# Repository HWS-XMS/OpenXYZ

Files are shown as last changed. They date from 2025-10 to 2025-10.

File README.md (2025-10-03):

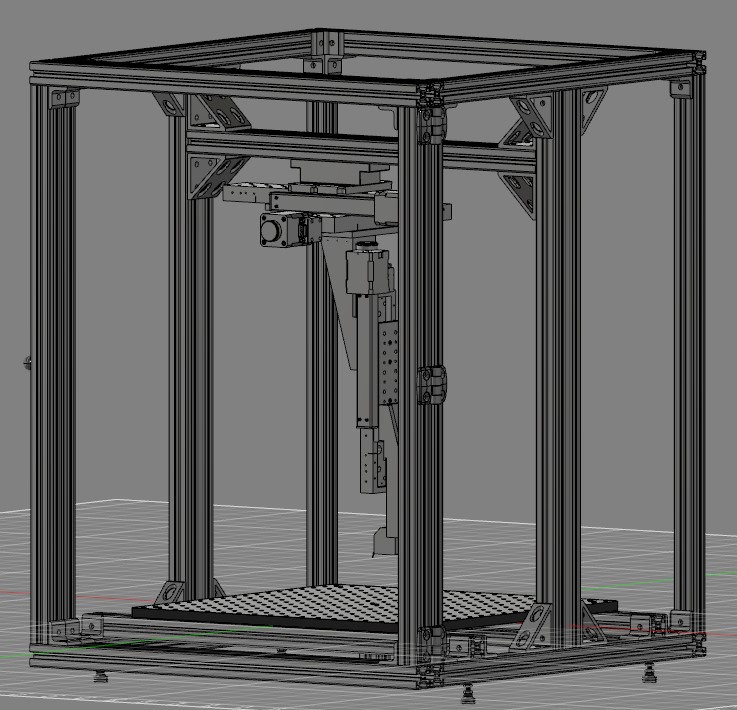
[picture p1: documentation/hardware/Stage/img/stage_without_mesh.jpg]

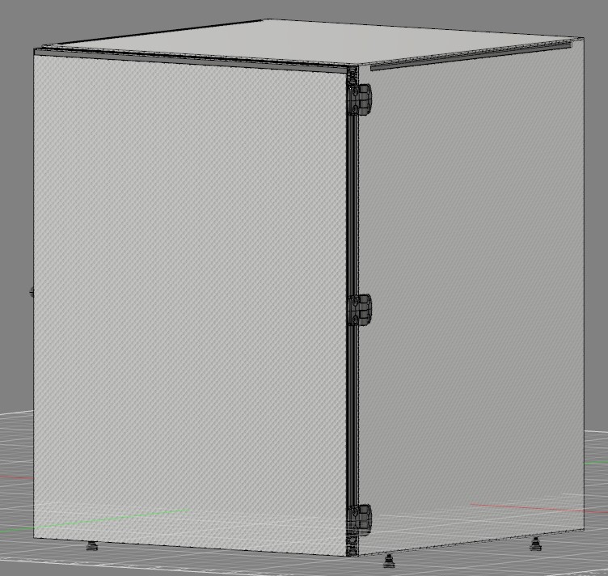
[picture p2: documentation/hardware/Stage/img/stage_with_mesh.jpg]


# Open-XYZ
An Open-Source Positioning System for Physical Attacks Exhibiting Spatial Resolution

**Author:** Marvin Sass
**Contributors:** Jakob Frömbgen, Olaf Durban

## Installation

### 1. Clone Repository with Submodules

```bash
git clone --recursive git@github.com:HWS-XMS/OpenXYZ.git
cd OpenXYZ
```

If you already cloned without `--recursive`:
```bash
git submodule update --init --recursive
```

### 2. Install Python Dependencies

**Host Computer:**
```bash
# Create and activate virtual environment (recommended)
python3 -m venv venv
source venv/bin/activate  # macOS/Linux
# .\venv\Scripts\activate  # Windows

# Install dependencies
pip3 install -r requirements.txt

# Install CoordinatePaths package from submodule
pip3 install -e CoordinatePaths/
```

**Raspberry Pi (for running the bridge server):**
```bash
pip3 install -r requirements-rpi.txt
```

## Path Generation

Path generation is handled by the separate [CoordinatePaths](https://github.com/HWS-XMS/CoordinatePaths) package (included as a git submodule). Three path types are available:

**RectangularPath** - Snake-like raster scanning:
```
(x_max, y_max)
  END +-->+-->+-->#
      ^   |   |   |
      +<--+<--+<--+
      |   |   |   ^
      +-->+-->+-->+
      ^   |   |   |
      +<--+<--+<--# START
                (0,0)
```

**CircularPath** - Spiral scanning from center outward

**PolygonPath** - Raster scanning within arbitrary polygonal areas

## Stage Positioning
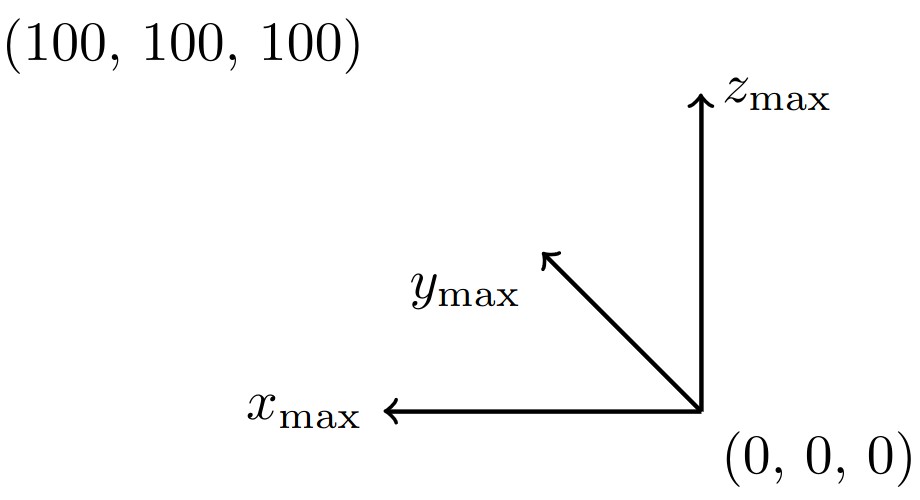
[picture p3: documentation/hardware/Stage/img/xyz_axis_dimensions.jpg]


The coordinate system origin is located at the bottom right (0, 0, 0). All coordinates are in millimeters. The stage supports 3-axis movement:
- **X/Y axes**: Horizontal positioning of probe
- **Z axis**: Height adjustment above target

## Usage

Complete working examples are available in the `examples/` directory:
- `basic_scan_with_callback.py` - Rectangular scanning with measurement callback
- `circular_scan_example.py` - Circular/spiral scanning pattern
- `read_scan_results.py` - Loading and processing saved measurement data

### Basic Example

```python
from openxyz.xyz_stage import Stage
from openxyz.marlin import Marlin
from coordinate_paths import RectangularPath
import decimal
import pickle

# Initialize stage
stage = Stage(Marlin(ip="openxyz"))  # or use IP address like "192.168.1.100"

# Create scanning path
path = RectangularPath(
    start_xy=(decimal.Decimal('0'), decimal.Decimal('0')),
    end_xy=(decimal.Decimal('10'), decimal.Decimal('10')),
    step_size_x=decimal.Decimal('0.5'),
    step_size_y=decimal.Decimal('0.5')
)

# Set probe height
stage.z = decimal.Decimal('40')

# Scan and measure
with open('results.pckl', 'wb') as f:
    for coordinate in path:
        # Move to position
        stage.x = coordinate[0]
        stage.y = coordinate[1]

        # Your measurement code here
        data = your_measurement_function()

        # Save with position
        pickle.dump((coordinate, data), f)
```

## Hardware Components

- **Motion Control**: Marlin firmware on BTT Manta M8P board
- **Actuators**: Motorized linear stages with TMC stepper drivers
- **Position Feedback**: LS7366R encoder chips with optical encoders
- **Control Interface**: Raspberry Pi running Flask server (optional bridge)

See `documentation/hardware/` for detailed hardware documentation.

## Architecture

**Host Computer** (your workstation):
- Runs measurement scripts
- Generates scan paths using CoordinatePaths
- Sends G-code commands to stage via HTTP

**Raspberry Pi** (optional bridge, runs `openxyz/rpi.py`):
- Flask HTTP server
- Converts HTTP requests to serial G-code
- Reads encoder positions via SPI
- Direct connection to Marlin controller

**Marlin Controller** (BTT Manta M8P):
- Executes G-code movement commands
- Controls stepper motors via TMC drivers
- Handles position tracking and limits

## License

MIT License

## Repository

https://github.com/HWS-XMS/OpenXYZ

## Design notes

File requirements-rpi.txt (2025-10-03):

# Open-XYZ Requirements (Raspberry Pi)
# Install with: pip install -r requirements-rpi.txt
#
# The Raspberry Pi runs the Flask server (rpi.py) that bridges HTTP to serial/encoder.
# Path generation and visualization happen on the host computer, not on the Pi.

# Core dependencies
pyserial>=3.5.0        # Serial communication with Marlin controller

# Raspberry Pi specific dependencies
RPi.GPIO>=0.7.1        # GPIO control for encoder chip select pins
spidev>=3.6.0          # SPI communication with LS7366R encoder chips
flask>=2.3.0           # HTTP server for Marlin/encoder API endpoints

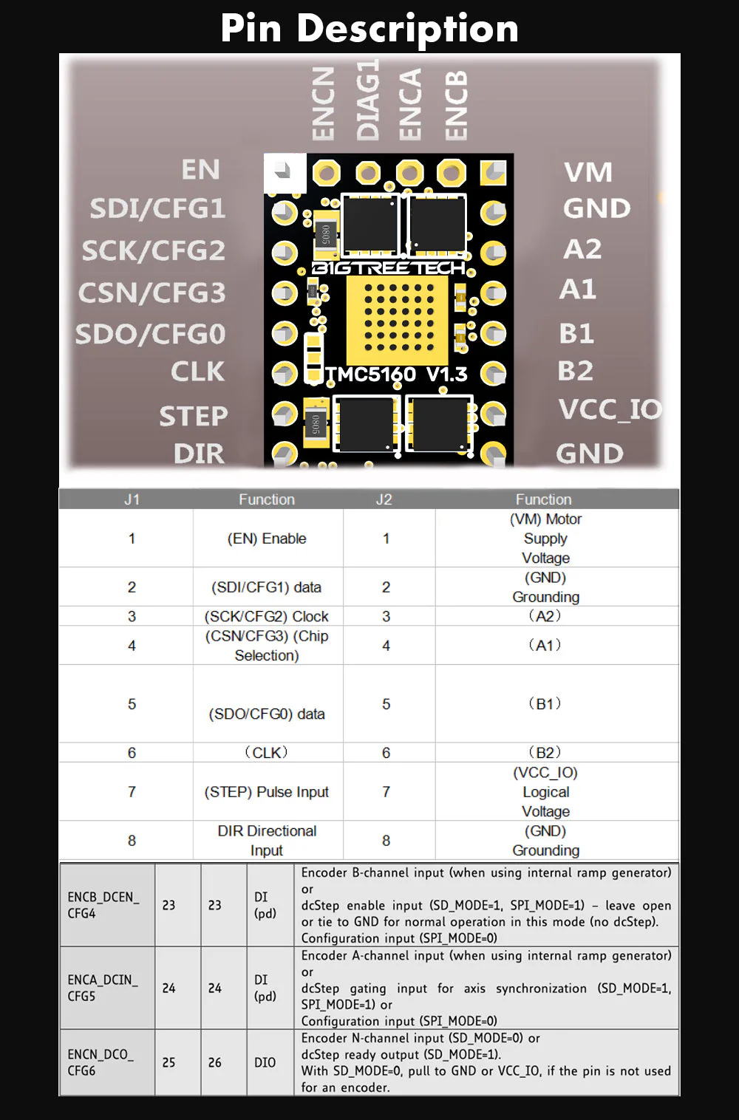
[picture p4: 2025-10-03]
documentation/hardware/TMC Drivers/TMC5160-data-sheet.webp

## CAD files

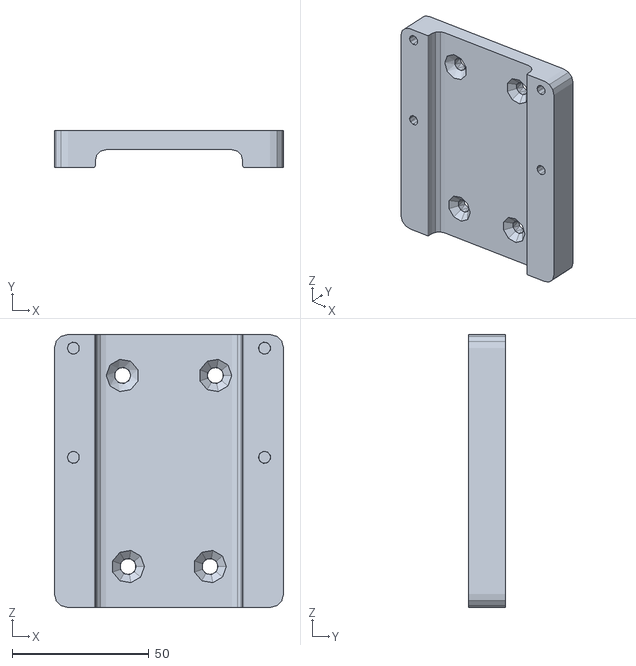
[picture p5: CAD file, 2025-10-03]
documentation/hardware/Chipshouter/cs_mount_bottom.stl
84.0 x 13.5 x 100.0

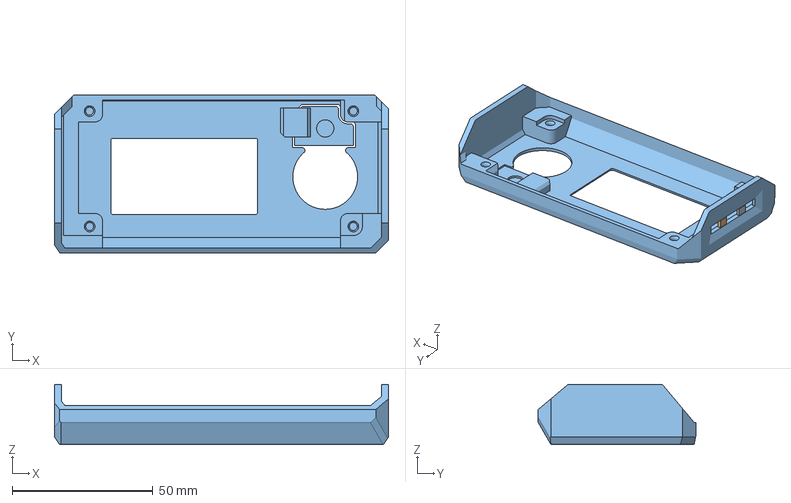
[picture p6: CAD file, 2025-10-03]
documentation/hardware/Display/new_cancel_button.3mf
118.7 x 56.0 x 21.5 mm
minidisplayhousing_v3 (1)
minidisplayhousing_v3 (2)
minidisplayhousing_v3

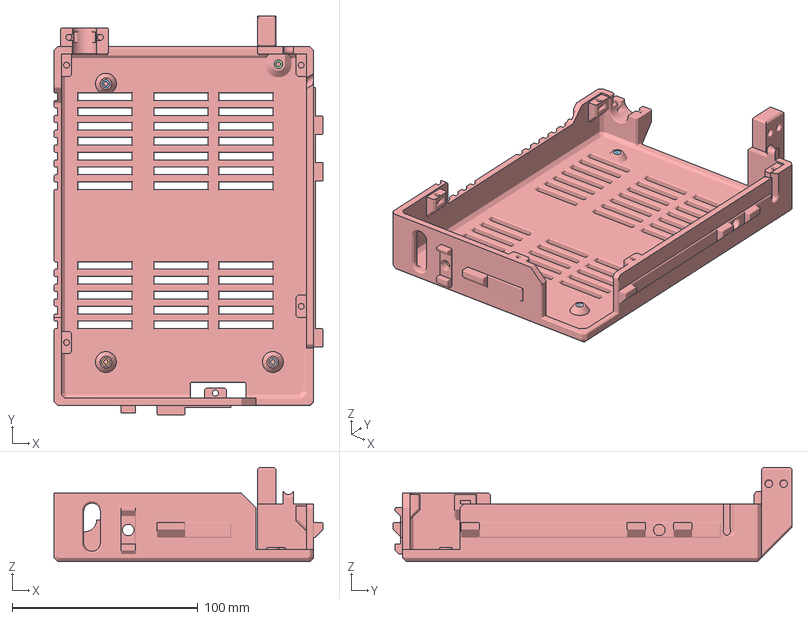
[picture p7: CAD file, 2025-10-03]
documentation/hardware/Manta Board/smaller_holes.3mf
145.0 x 214.9 x 50.7 mm
M8P Caribou - Unterteil

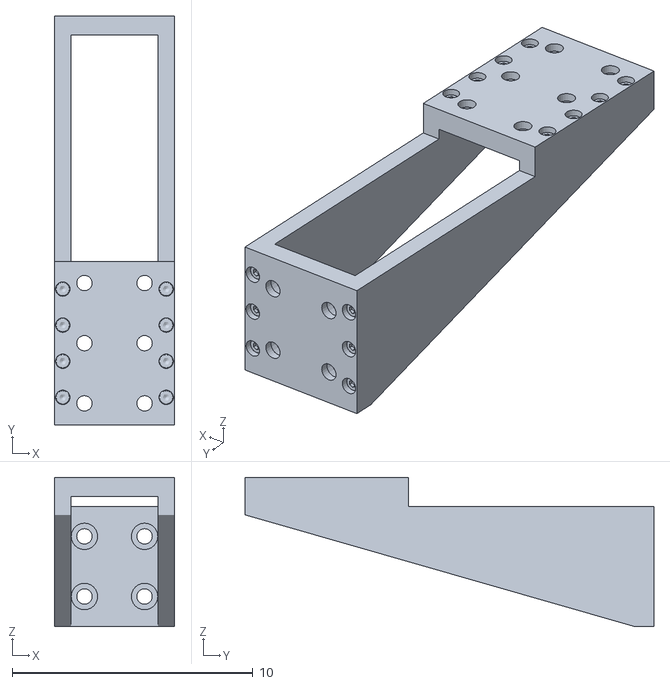
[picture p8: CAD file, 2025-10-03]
documentation/hardware/Stage/2AB175_90_degree_angle_bracket.obj
5.00 x 17.0 x 6.20

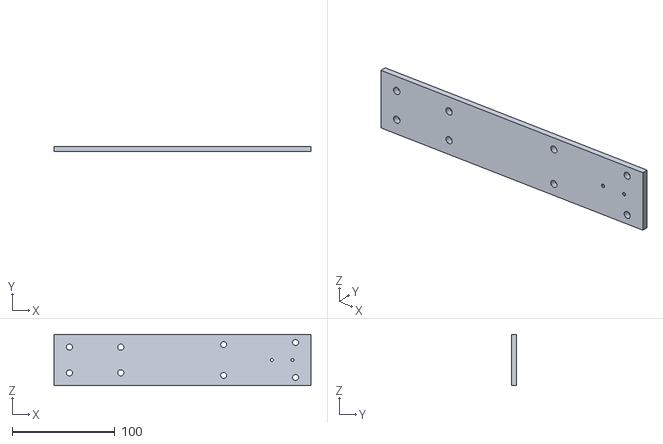
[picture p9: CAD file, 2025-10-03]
documentation/hardware/Chipshouter/cs_adapter.stl
250.0 x 5.00 x 50.0

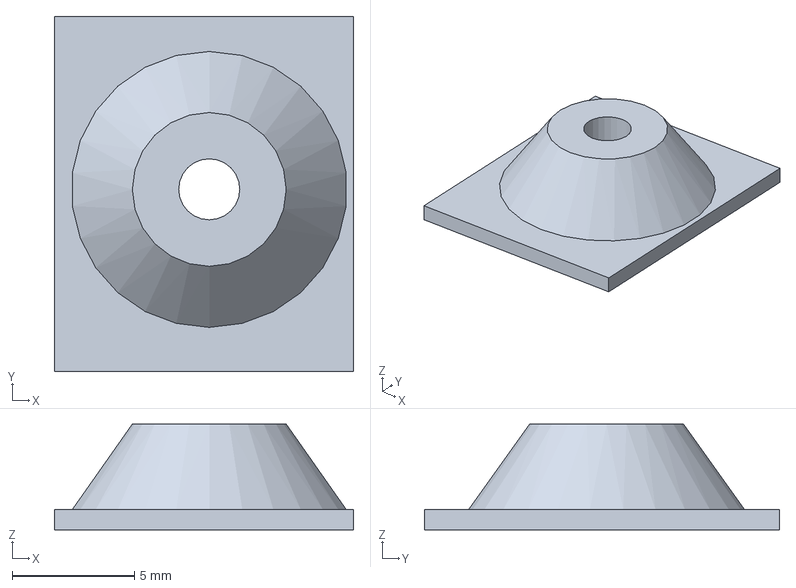
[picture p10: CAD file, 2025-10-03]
documentation/hardware/Manta Board/hole_test.3mf
12.3 x 14.5 x 4.34 mm

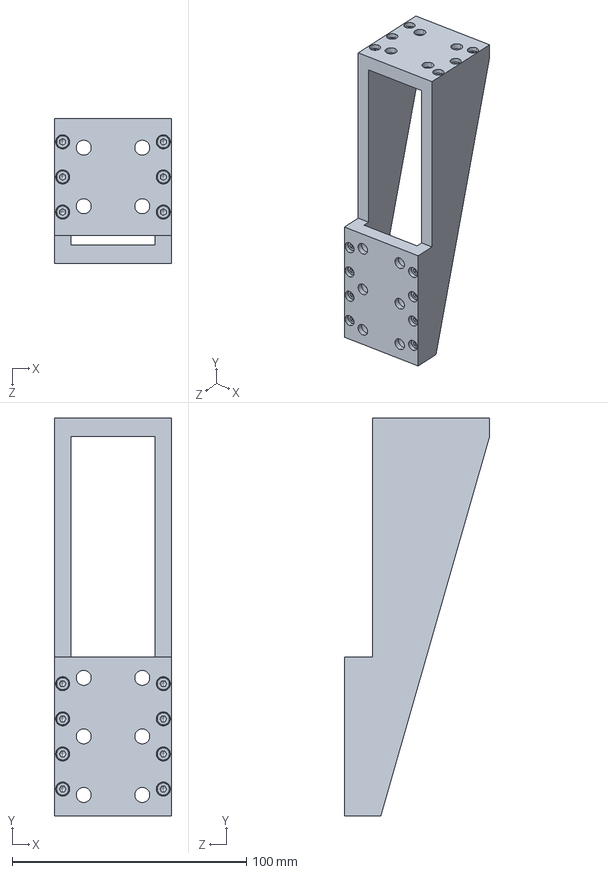
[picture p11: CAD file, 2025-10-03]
documentation/hardware/Stage/2AB175.STEP
50.0 x 170.0 x 62.0 mm

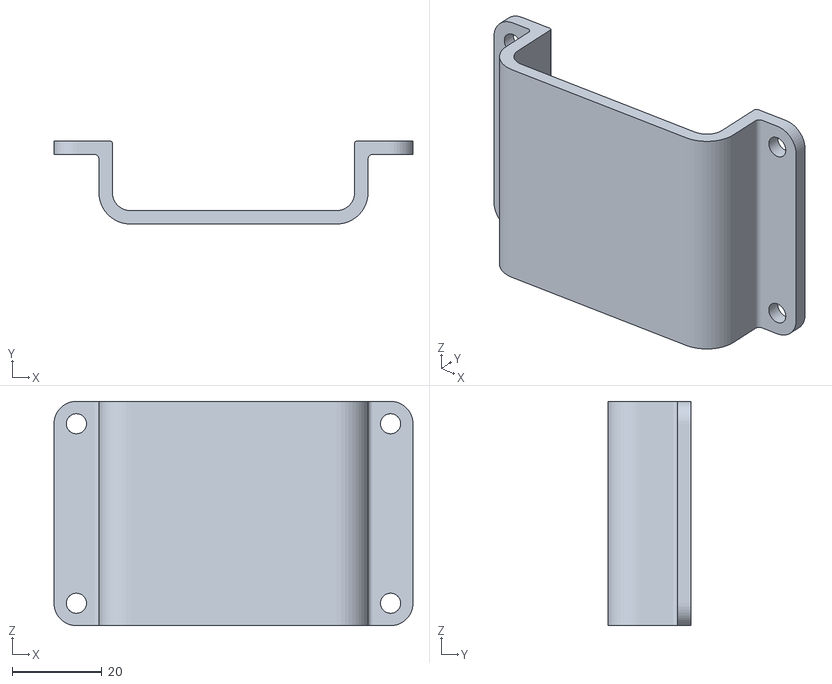
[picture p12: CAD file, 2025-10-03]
documentation/hardware/Chipshouter/cs_mount_top.stl
80.0 x 18.5 x 50.0

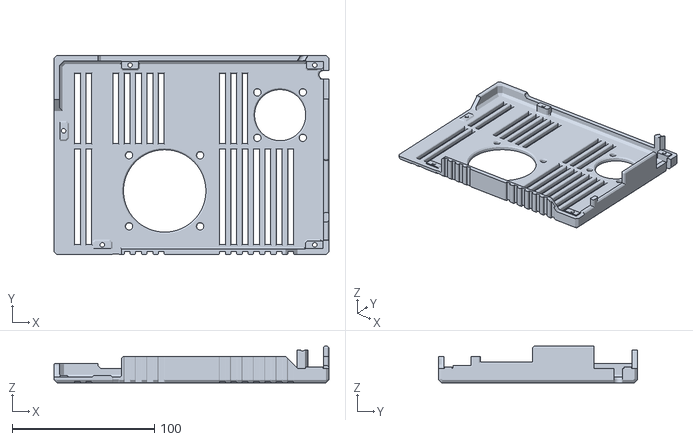
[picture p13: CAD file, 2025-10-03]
documentation/hardware/Manta Board/M8P Caribou - Deckel.stl
193.5 x 140.0 x 25.7

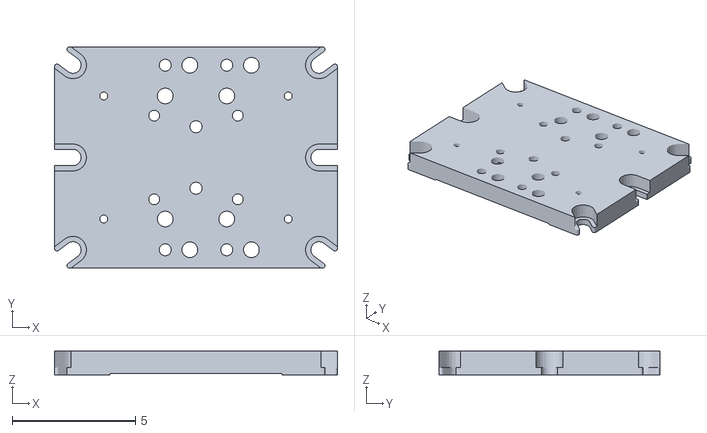
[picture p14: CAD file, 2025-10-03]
documentation/hardware/Stage/3UBP175__Baseplate_for_linear_actuators.obj
11.5 x 9.00 x 0.97

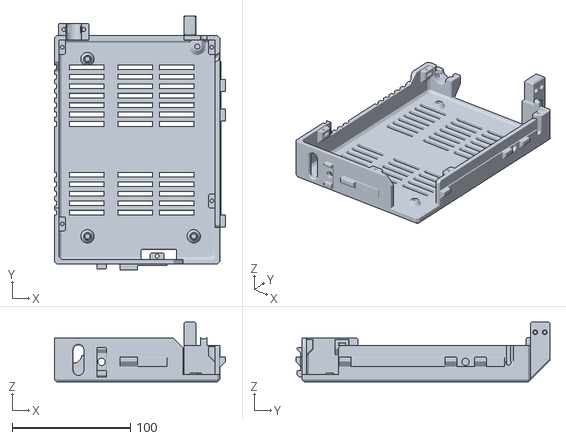
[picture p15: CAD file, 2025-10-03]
documentation/hardware/Manta Board/M8P Caribou - Unterteil.stl
145.0 x 214.9 x 50.7

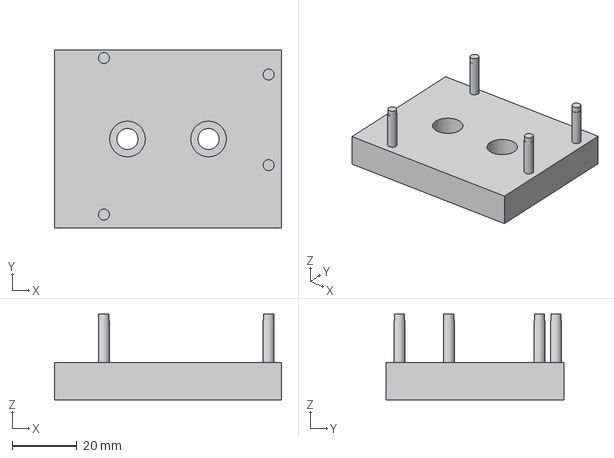
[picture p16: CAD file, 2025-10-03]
documentation/hardware/Stage/simple_Arduino_UNO_mount.3mf
70.0 x 55.0 x 26.5 mm

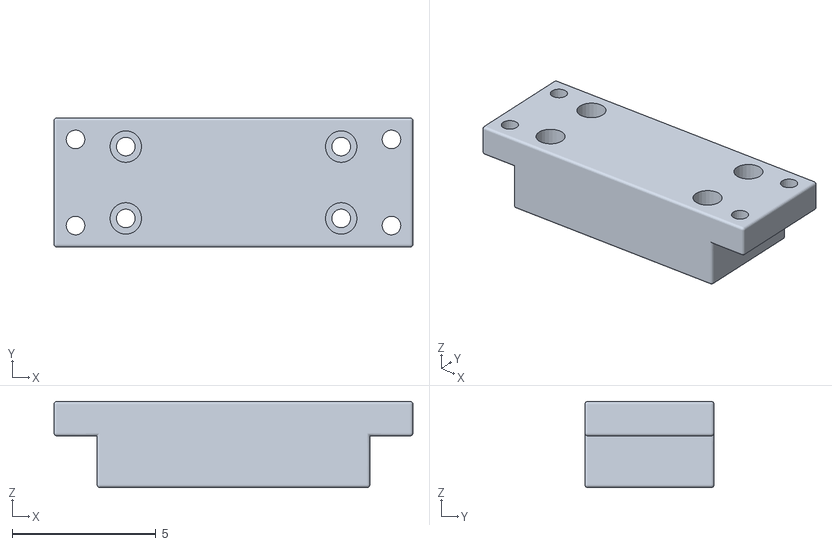
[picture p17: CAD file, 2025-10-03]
documentation/hardware/Stage/adapter_v4.obj
12.5 x 4.50 x 3.00

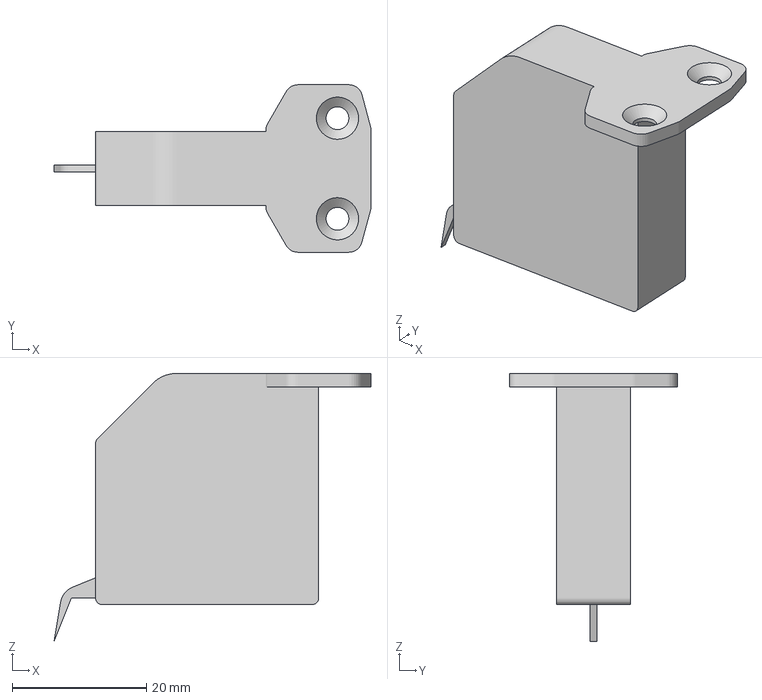
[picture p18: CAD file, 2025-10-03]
documentation/hardware/Stage/Probe Dummy 3D model 6.2x5.5 ICR v1.3mf
47.3 x 25.0 x 40.0 mm

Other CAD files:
documentation/hardware/Display/minidisplayhousing_v3.stl
documentation/hardware/Stage/3UBP175.STEP
documentation/hardware/Stage/Halterung Probe v3.3mf
documentation/hardware/Stage/Probe Dummy 3D model 6.2x5.5 ICR v1.obj

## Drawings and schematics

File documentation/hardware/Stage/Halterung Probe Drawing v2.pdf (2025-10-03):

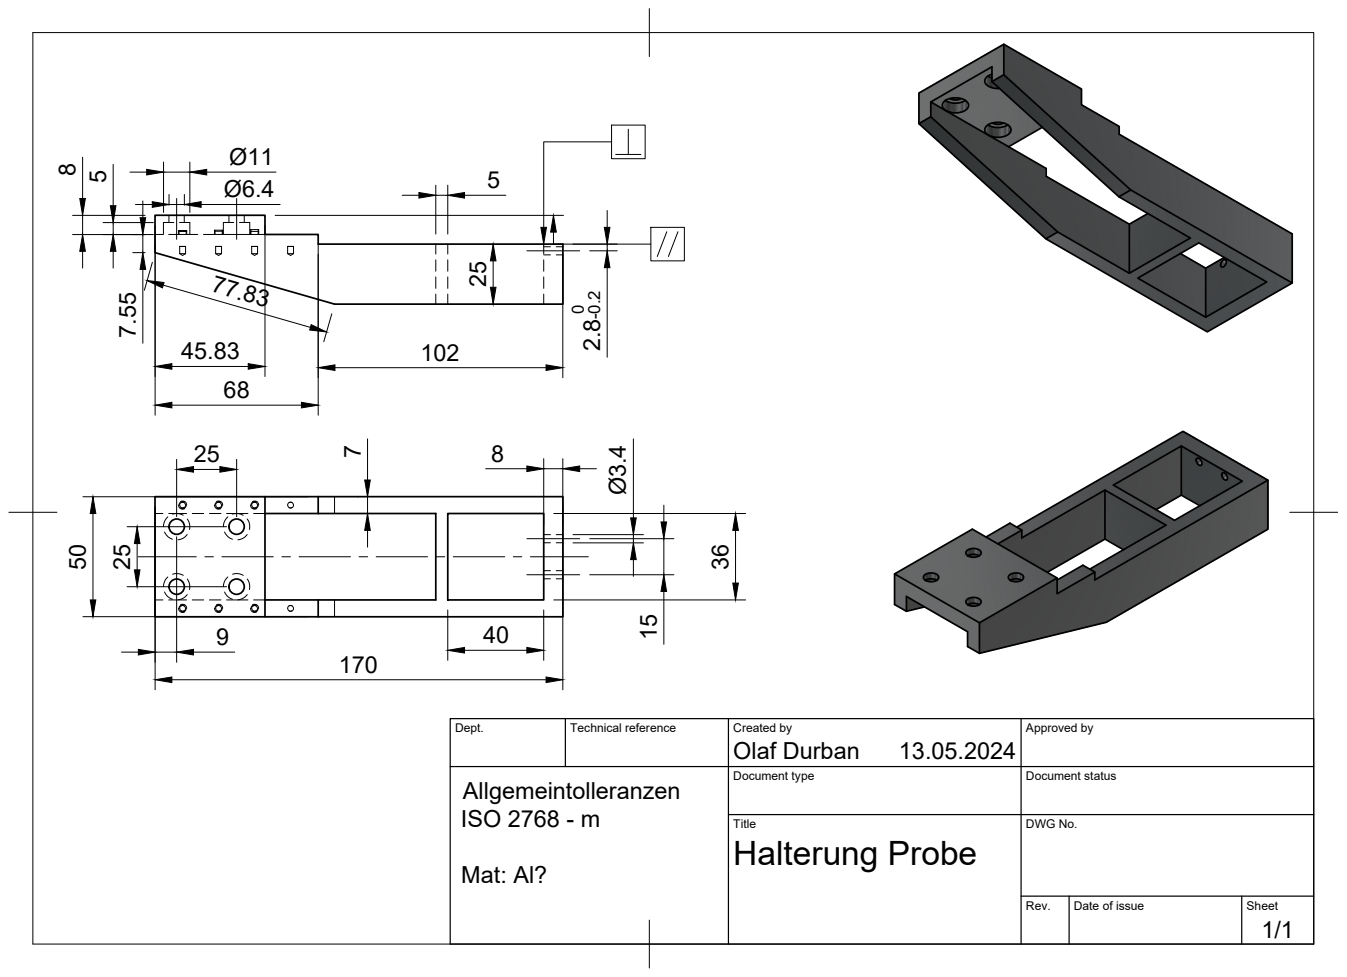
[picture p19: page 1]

Dept. | Technical reference | Created by Olaf Durban 13.05.2024 | Approved by

Allgemeintolleranzen ISO 2768 - m Mat: Al? | | Document type | Document status

Title Halterung Probe | DWG No.

Rev. | Date of issue | Sheet 1/1

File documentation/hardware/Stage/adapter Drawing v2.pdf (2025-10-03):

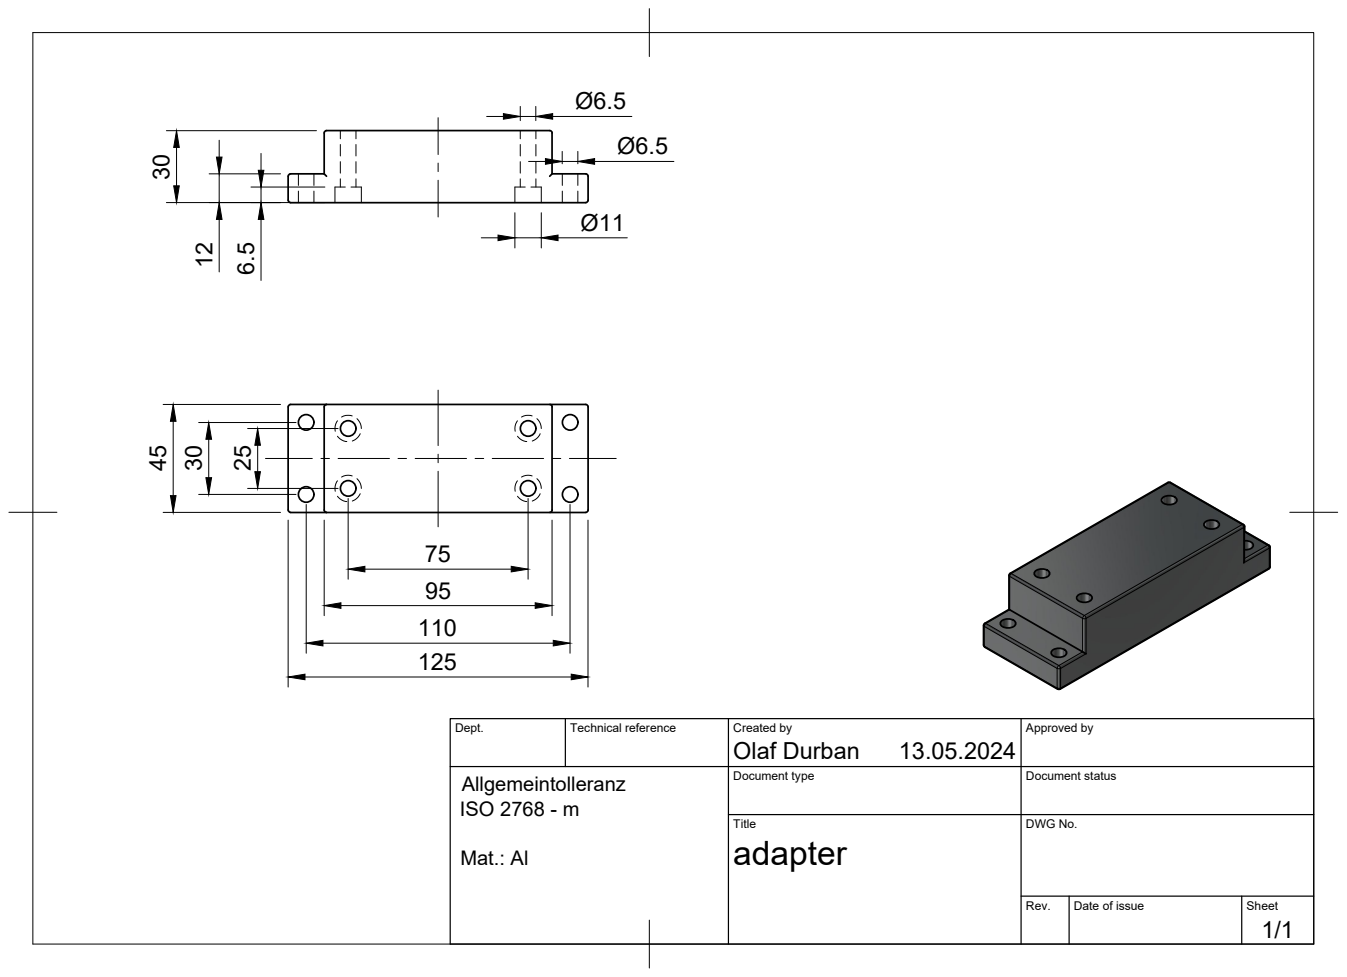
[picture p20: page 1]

Dept. | Technical reference | Created by Olaf Durban 13.05.2024 | Approved by

Allgemeintolleranz ISO 2768 - m Mat.: Al | | Document type | Document status

Title adapter | DWG No.

Rev. | Date of issue | Sheet 1/1

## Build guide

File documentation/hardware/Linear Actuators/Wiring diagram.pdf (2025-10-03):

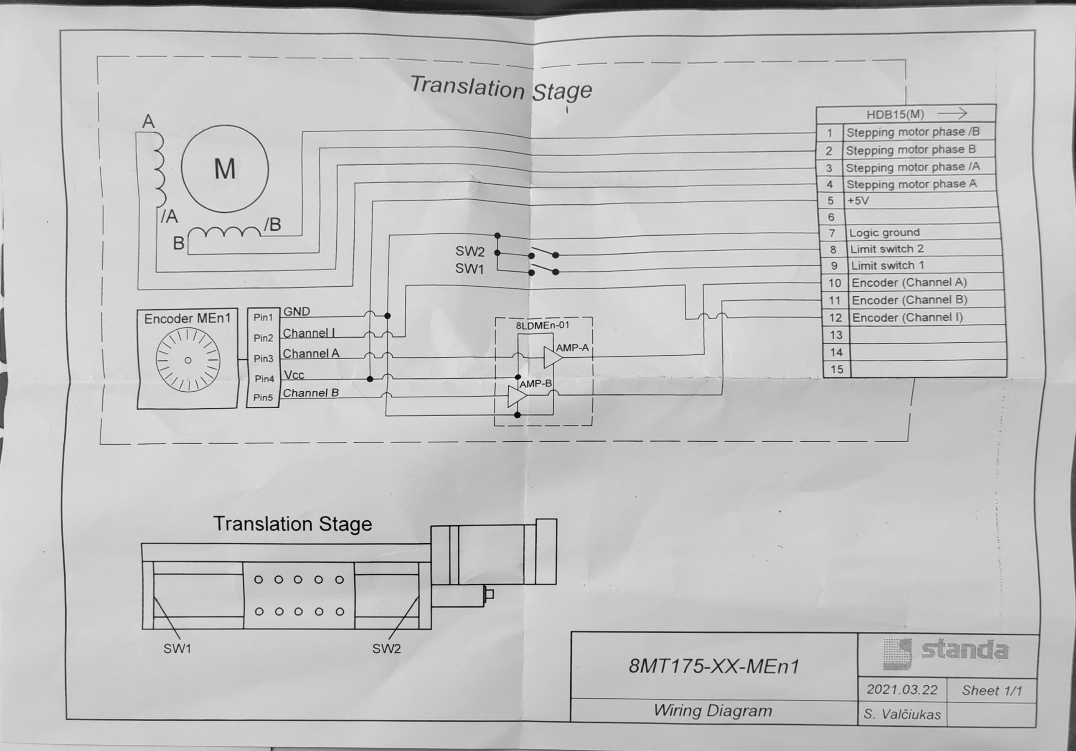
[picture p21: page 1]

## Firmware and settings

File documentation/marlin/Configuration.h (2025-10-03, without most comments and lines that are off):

#pragma once
#define CONFIGURATION_H_VERSION 02010300
#define STRING_CONFIG_H_AUTHOR "(none, default config)" // Who made the changes.
  #define MOTHERBOARD BOARD_BTT_MANTA_M8P_V2_0
#define SERIAL_PORT -1
#define BAUDRATE 250000
#define X_DRIVER_TYPE  TMC5160
#define Y_DRIVER_TYPE  TMC5160
#define Z_DRIVER_TYPE  TMC5160
#define EXTRUDERS 0
#define DEFAULT_NOMINAL_FILAMENT_DIA 1.75
#define TEMP_SENSOR_0 1
#define TEMP_SENSOR_1 0
#define TEMP_SENSOR_2 0
#define TEMP_SENSOR_3 0
#define TEMP_SENSOR_4 0
#define TEMP_SENSOR_5 0
#define TEMP_SENSOR_6 0
#define TEMP_SENSOR_7 0
#define TEMP_SENSOR_BED 0
#define TEMP_SENSOR_PROBE 0
#define TEMP_SENSOR_CHAMBER 0
#define TEMP_SENSOR_COOLER 0
#define TEMP_SENSOR_BOARD 0
#define TEMP_SENSOR_SOC 0
#define TEMP_SENSOR_REDUNDANT 0
#define DUMMY_THERMISTOR_998_VALUE  25
#define DUMMY_THERMISTOR_999_VALUE 100
#if TEMP_SENSOR_IS_MAX_TC(0)
  #define MAX31865_SENSOR_OHMS_0      100 // (Ω) Typically 100 or 1000 (PT100 or PT1000)
  #define MAX31865_CALIBRATION_OHMS_0 430 // (Ω) Typically 430 for Adafruit PT100; 4300 for Adafruit PT1000
#endif
#if TEMP_SENSOR_IS_MAX_TC(1)
  #define MAX31865_SENSOR_OHMS_1      100
  #define MAX31865_CALIBRATION_OHMS_1 430
#endif
#if TEMP_SENSOR_IS_MAX_TC(2)
  #define MAX31865_SENSOR_OHMS_2      100
  #define MAX31865_CALIBRATION_OHMS_2 430
#endif
#if HAS_E_TEMP_SENSOR
  #define TEMP_RESIDENCY_TIME         10  // (seconds) Time to wait for hotend to "settle" in M109
  #define TEMP_WINDOW                  1  // (°C) Temperature proximity for the "temperature reached" timer
  #define TEMP_HYSTERESIS              3  // (°C) Temperature proximity considered "close enough" to the target
#endif
#if TEMP_SENSOR_BED
  #define TEMP_BED_RESIDENCY_TIME     10  // (seconds) Time to wait for bed to "settle" in M190
  #define TEMP_BED_WINDOW              1  // (°C) Temperature proximity for the "temperature reached" timer
  #define TEMP_BED_HYSTERESIS          3  // (°C) Temperature proximity considered "close enough" to the target
#endif
#if TEMP_SENSOR_CHAMBER
  #define TEMP_CHAMBER_RESIDENCY_TIME 10  // (seconds) Time to wait for chamber to "settle" in M191
  #define TEMP_CHAMBER_WINDOW          1  // (°C) Temperature proximity for the "temperature reached" timer
  #define TEMP_CHAMBER_HYSTERESIS      3  // (°C) Temperature proximity considered "close enough" to the target
#endif
#if TEMP_SENSOR_REDUNDANT
  #define TEMP_SENSOR_REDUNDANT_SOURCE    E1  // The sensor that will provide the redundant reading.
  #define TEMP_SENSOR_REDUNDANT_TARGET    E0  // The sensor that we are providing a redundant reading for.
  #define TEMP_SENSOR_REDUNDANT_MAX_DIFF  10  // (°C) Temperature difference that will trigger a print abort.
#endif
#define HEATER_0_MINTEMP   5
#define HEATER_1_MINTEMP   5
#define HEATER_2_MINTEMP   5
#define HEATER_3_MINTEMP   5
#define HEATER_4_MINTEMP   5
#define HEATER_5_MINTEMP   5
#define HEATER_6_MINTEMP   5
#define HEATER_7_MINTEMP   5
#define BED_MINTEMP        5
#define CHAMBER_MINTEMP    5
#define HEATER_0_MAXTEMP 275
#define HEATER_1_MAXTEMP 275
#define HEATER_2_MAXTEMP 275
#define HEATER_3_MAXTEMP 275
#define HEATER_4_MAXTEMP 275
#define HEATER_5_MAXTEMP 275
#define HEATER_6_MAXTEMP 275
#define HEATER_7_MAXTEMP 275
#define BED_MAXTEMP      150
#define CHAMBER_MAXTEMP  60
#define HOTEND_OVERSHOOT 15   // (°C) Forbid temperatures over MAXTEMP - OVERSHOOT
#define BED_OVERSHOOT    10   // (°C) Forbid temperatures over MAXTEMP - OVERSHOOT
#define COOLER_OVERSHOOT  2   // (°C) Forbid temperatures closer than OVERSHOOT
#define PIDTEMP           // See the PID Tuning Guide at https://reprap.org/wiki/PID_Tuning
#define PID_MAX  255      // Limit hotend current while PID is active (see PID_FUNCTIONAL_RANGE below); 255=full current
#define PID_K1     0.95   // Smoothing factor within any PID loop
    #define DEFAULT_Kp  22.20
    #define DEFAULT_Ki   1.08
    #define DEFAULT_Kd 114.00
#define MAX_BED_POWER 255 // limits duty cycle to bed; 255=full current
#define MAX_CHAMBER_POWER 255 // limits duty cycle to chamber heater; 255=full current
  #define PID_FUNCTIONAL_RANGE 10 // If the temperature difference between the target temperature and the actual temperature
#define PREVENT_LENGTHY_EXTRUDE
#define EXTRUDE_MAXLENGTH 200
#define ENDSTOPPULLUPS
#define X_MIN_ENDSTOP_HIT_STATE LOW
#define X_MAX_ENDSTOP_HIT_STATE LOW
#define Y_MIN_ENDSTOP_HIT_STATE LOW
#define Y_MAX_ENDSTOP_HIT_STATE LOW
#define Z_MIN_ENDSTOP_HIT_STATE LOW
#define Z_MAX_ENDSTOP_HIT_STATE LOW
#define I_MIN_ENDSTOP_HIT_STATE HIGH
#define I_MAX_ENDSTOP_HIT_STATE HIGH
#define J_MIN_ENDSTOP_HIT_STATE HIGH
#define J_MAX_ENDSTOP_HIT_STATE HIGH
#define K_MIN_ENDSTOP_HIT_STATE HIGH
#define K_MAX_ENDSTOP_HIT_STATE HIGH
#define U_MIN_ENDSTOP_HIT_STATE HIGH
#define U_MAX_ENDSTOP_HIT_STATE HIGH
#define V_MIN_ENDSTOP_HIT_STATE HIGH
#define V_MAX_ENDSTOP_HIT_STATE HIGH
#define W_MIN_ENDSTOP_HIT_STATE HIGH
#define W_MAX_ENDSTOP_HIT_STATE HIGH
#define Z_MIN_PROBE_ENDSTOP_HIT_STATE HIGH
#define DEFAULT_AXIS_STEPS_PER_UNIT   { 6400, 6400, 6400 }
#define EDITABLE_STEPS_PER_UNIT
#define DEFAULT_MAX_FEEDRATE          { 5, 5, 5 }
#define DEFAULT_MAX_ACCELERATION      { 1, 1, 1 }
#define DEFAULT_ACCELERATION          1    // X, Y, Z and E acceleration for printing moves
#define DEFAULT_RETRACT_ACCELERATION  1    // E acceleration for retracts
#define DEFAULT_TRAVEL_ACCELERATION   1    // X, Y, Z acceleration for travel (non printing) moves
  #define JUNCTION_DEVIATION_MM 0.013 // (mm) Distance from real junction edge
  #define JD_HANDLE_SMALL_SEGMENTS    // Use curvature estimation instead of just the junction angle
#define Z_MIN_PROBE_USES_Z_MIN_ENDSTOP_PIN
#define NOZZLE_TO_PROBE_OFFSET { 10, 10, 0 }
#define PROBING_TOOL 0
#define PROBING_MARGIN 10
#define XY_PROBE_FEEDRATE (100)
#define Z_PROBE_FEEDRATE_FAST (100)
#define Z_PROBE_FEEDRATE_SLOW (Z_PROBE_FEEDRATE_FAST / 2)
#define Z_CLEARANCE_DEPLOY_PROBE   10 // (mm) Z Clearance for Deploy/Stow
#define Z_CLEARANCE_BETWEEN_PROBES  5 // (mm) Z Clearance between probe points
#define Z_CLEARANCE_MULTI_PROBE     5 // (mm) Z Clearance between multiple probes
#define Z_PROBE_ERROR_TOLERANCE     3 // (mm) Tolerance for early trigger (<= -probe.offset.z + ZPET)
#define Z_PROBE_LOW_POINT          -2 // (mm) Farthest distance below the trigger-point to go before stopping
#define X_ENABLE_ON 0
#define Y_ENABLE_ON 0
#define Z_ENABLE_ON 0
#define E_ENABLE_ON 0 // For all extruders
#define DISABLE_OTHER_EXTRUDERS   // Keep only the active extruder enabled
#define INVERT_X_DIR false // false
#define INVERT_Y_DIR false // true
#define INVERT_Z_DIR true // false
#define INVERT_E0_DIR false
#define INVERT_E1_DIR false
#define INVERT_E2_DIR false
#define INVERT_E3_DIR false
#define INVERT_E4_DIR false
#define INVERT_E5_DIR false
#define INVERT_E6_DIR false
#define INVERT_E7_DIR false
#define X_HOME_DIR -1
#define Y_HOME_DIR -1
#define Z_HOME_DIR 1
#define X_SAFETY_STOP
#define Y_SAFETY_STOP
#define Z_SAFETY_STOP
#define X_BED_SIZE 100
#define Y_BED_SIZE 100
#define X_MIN_POS 0
#define Y_MIN_POS 0
#define Z_MIN_POS 0
#define X_MAX_POS X_BED_SIZE
#define Y_MAX_POS Y_BED_SIZE
#define Z_MAX_POS 100
#define MIN_SOFTWARE_ENDSTOPS
  #define MIN_SOFTWARE_ENDSTOP_X
  #define MIN_SOFTWARE_ENDSTOP_Y
  #define MIN_SOFTWARE_ENDSTOP_Z
  #define MIN_SOFTWARE_ENDSTOP_I
  #define MIN_SOFTWARE_ENDSTOP_J
  #define MIN_SOFTWARE_ENDSTOP_K
  #define MIN_SOFTWARE_ENDSTOP_U
  #define MIN_SOFTWARE_ENDSTOP_V
  #define MIN_SOFTWARE_ENDSTOP_W
#define MAX_SOFTWARE_ENDSTOPS
  #define MAX_SOFTWARE_ENDSTOP_X
  #define MAX_SOFTWARE_ENDSTOP_Y
  #define MAX_SOFTWARE_ENDSTOP_Z
  #define MAX_SOFTWARE_ENDSTOP_I
  #define MAX_SOFTWARE_ENDSTOP_J
  #define MAX_SOFTWARE_ENDSTOP_K
  #define MAX_SOFTWARE_ENDSTOP_U
  #define MAX_SOFTWARE_ENDSTOP_V
  #define MAX_SOFTWARE_ENDSTOP_W
  #define SOFT_ENDSTOPS_MENU_ITEM  // Enable/Disable software endstops from the LCD
#define HOMING_FEEDRATE_MM_M { (2*60), (2*60), (2*60) }
#define VALIDATE_HOMING_ENDSTOPS
#define EEPROM_SETTINGS     // Persistent storage with M500 and M501
#define EEPROM_CHITCHAT       // Give feedback on EEPROM commands. Disable to save flash.
#define EEPROM_BOOT_SILENT    // Keep M503 quiet and only give errors during first load
#define HOST_KEEPALIVE_FEATURE        // Disable this if your host doesn't like keepalive messages
#define DEFAULT_KEEPALIVE_INTERVAL 2  // Number of seconds between "busy" messages. Set with M113.
#define BUSY_WHILE_HEATING            // Some hosts require "busy" messages even during heating
#define PREHEAT_1_LABEL       "PLA"
#define PREHEAT_1_TEMP_HOTEND 180
#define PREHEAT_1_TEMP_BED     70
#define PREHEAT_1_TEMP_CHAMBER 35
#define PREHEAT_1_FAN_SPEED     0 // Value from 0 to 255
#define PREHEAT_2_LABEL       "ABS"
#define PREHEAT_2_TEMP_HOTEND 240
#define PREHEAT_2_TEMP_BED    110
#define PREHEAT_2_TEMP_CHAMBER 35
#define PREHEAT_2_FAN_SPEED     0 // Value from 0 to 255
#define PRINTJOB_TIMER_AUTOSTART
#define PASSWORD_FEATURE
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

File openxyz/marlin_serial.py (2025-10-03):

# EMFI Station - Orchestrate electromagnetic fault injection attacks
# Copyright (C) 2022 Niclas Kühnapfel
#
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
import time
import serial
import logging

BUSY_MSG = b'echo:busy: processing\n'
OK_MSG = b'ok\n'


class MarlinSerial:
	"""
	Manages serial connection to Marlin-based controller board.

	:param tty: Serial port (e.g.: '/dev/ttyACM0')
	:type tty: str
	:param mock: If True, use a mock serial connection
	:type mock: bool, optional
	"""

	def __init__(self, tty: str, mock: bool = False):
		self.log = logging.getLogger(__name__)
		self.sim = mock
		if not self.sim:
			self.ser = serial.Serial(port=tty, baudrate=115200, timeout=0.25)
			self.clear()

	def clear(self) -> None:
		"""
		Clears serial input buffer.

		:return: None
		:rtype: None
		"""
		if self.sim:
			self.log.info('Clearing serial buffer.')
		else:
			self.ser.flush()
			self.ser.reset_input_buffer()

	def read(self) -> bytes:
		"""
		Reads a line from serial interface.

		:return: Line read from serial interface
		:rtype: bytes
		"""
		if self.sim:
			time.sleep(0.5)
			return b'ok\n'
		else:
			msg = self.ser.readline()
			self.log.debug('Read from serial port: {:s}'.format(str(msg)))
			return msg

	def close(self) -> None:
		"""
		Closes serial port.

		:return: None
		:rtype: None
		"""
		self.log.info('Closing serial port.')
		if not self.sim:
			self.ser.close()

	def send_gcode(self, cmd: str) -> bytes:
		"""
		Sends command via serial.

		:param cmd: Command string (e.g.: 'M122')
		:return: None
		"""
		if self.sim:
			self.log.info('Sending: {:s}'.format(str(cmd)))
		else:
			self.log.debug('Write to serial port: {:s}'.format(str(cmd)))
			self.ser.write((cmd + '\n').encode())
			self.ser.flush()
		response = self.__wait_cmd_completed()

		# if command is a movement command, wait for it to be completed
		if cmd.startswith('G0') or cmd.startswith('G1'):
			self.__wait_move_completed()

		return response

	def emergency(self) -> None:
		"""
		Stops movement immediately but allows further commands (M410).

		:return: None
		:rtype: None
		"""
		self.send_gcode('M410')
		self.log.critical('Emergency stop initiated.')
		self.__wait_cmd_completed()

	def __wait_cmd_completed(self, max_tries: int = 100) -> bytes:
		"""
		Waits for a command to be completed.
		HOST_KEEPALIVE_FEATURE has to be enabled in Marlin configuration.
		Marlin is expected to send a 'busy' message once a second (DEFAULT_KEEPALIVE_INTERVAL 1).

		:param max_tries: Maximum number of tries to receive 'ok' message.
		:type max_tries: int
		:return: All received messages
		:rtype: bytes
		"""
		msg = b''
		try:
			counter = 0
			while True:
				res = self.ser.read()
				if res:
					msg += res
				if BUSY_MSG in msg:
					counter = 0
					msg = b''
				if OK_MSG in msg:
					break
				counter += 1
				if counter > max_tries:
					raise IOError('Timeout while waiting for a command to be completed: {:s}'.format(str(msg)))
		except KeyboardInterrupt:
			self.emergency()
			raise

		return msg + self.ser.read()

	def __wait_move_completed(self) -> None:
		"""
		Waits for movement to be completed (M400).

		:return: None
		:rtype: None
		"""
		self.clear()
		self.send_gcode('M400')


if __name__ == "__main__":
	# Example usage
	logging.basicConfig(level=logging.DEBUG)
	ser = MarlinSerial('/dev/ttyACM0', mock=False)
	r = ser.send_gcode('G91').decode('utf-8').replace('ok\n', '')
	print("\t", r)
	ser.close()

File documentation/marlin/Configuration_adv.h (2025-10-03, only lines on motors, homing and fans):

#define E0_AUTO_FAN_PIN -1
#define E1_AUTO_FAN_PIN -1
#define E2_AUTO_FAN_PIN -1
#define E3_AUTO_FAN_PIN -1
#define E4_AUTO_FAN_PIN -1
#define E5_AUTO_FAN_PIN -1
#define E6_AUTO_FAN_PIN -1
#define E7_AUTO_FAN_PIN -1
#define CHAMBER_AUTO_FAN_PIN -1
#define COOLER_AUTO_FAN_PIN -1
#define HOMING_BUMP_MM      { 2, 2, 2 }       // (linear=mm, rotational=°) Backoff from endstops after first bump
#define HOMING_BUMP_DIVISOR { 4, 4, 4 }       // Re-Bump Speed Divisor (Divides the Homing Feedrate)
#define MICROSTEP_MODES { 16, 16, 16, 16, 16, 16 } // [1,2,4,8,16]
    #define X_CURRENT       800        // (mA) RMS current. Multiply by 1.414 for peak current.
    #define X_CURRENT_HOME  X_CURRENT  // (mA) RMS current for sensorless homing
    #define X_MICROSTEPS     16        // 0..256
    #define Y_CURRENT       800
    #define Y_CURRENT_HOME  Y_CURRENT
    #define Y_MICROSTEPS     16
    #define Z_CURRENT       800
    #define Z_CURRENT_HOME  Z_CURRENT
    #define Z_MICROSTEPS     16
    #define CURRENT_STEP_DOWN     50  // [mA]
    #define REPORT_CURRENT_CHANGE
  #define X_HYBRID_THRESHOLD     100  // [mm/s]
  #define X2_HYBRID_THRESHOLD    100
  #define Y_HYBRID_THRESHOLD     100
  #define Y2_HYBRID_THRESHOLD    100
  #define Z_HYBRID_THRESHOLD       3
  #define Z2_HYBRID_THRESHOLD      3
  #define Z3_HYBRID_THRESHOLD      3
  #define Z4_HYBRID_THRESHOLD      3
  #define I_HYBRID_THRESHOLD       3  // [linear=mm/s, rotational=°/s]
  #define J_HYBRID_THRESHOLD       3  // [linear=mm/s, rotational=°/s]
  #define K_HYBRID_THRESHOLD       3  // [linear=mm/s, rotational=°/s]
  #define U_HYBRID_THRESHOLD       3  // [mm/s]
  #define V_HYBRID_THRESHOLD       3
  #define W_HYBRID_THRESHOLD       3
  #define E0_HYBRID_THRESHOLD     30
  #define E1_HYBRID_THRESHOLD     30
  #define E2_HYBRID_THRESHOLD     30
  #define E3_HYBRID_THRESHOLD     30
  #define E4_HYBRID_THRESHOLD     30
  #define E5_HYBRID_THRESHOLD     30
  #define E6_HYBRID_THRESHOLD     30
  #define E7_HYBRID_THRESHOLD     30

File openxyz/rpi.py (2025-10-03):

# Open-XYZ - An Open-Source Positioning System for Physical Attacks Exhibiting Spatial Resolution
# Copyright (C) 2024 Jakob Frömbgen
#
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
from flask import Flask, request, jsonify
import serial
import logging

from openxyz.marlin_serial 	import MarlinSerial
from openxyz.encoder 		import LS7366R, EncoderAxis

app = Flask(__name__)

enc = LS7366R(bus=0, cs_pins={
	EncoderAxis.ENCODER_AXIS_X: 23,
	EncoderAxis.ENCODER_AXIS_Y: 24
})

# Configure logging
logging.basicConfig(level=logging.DEBUG)
logger = logging.getLogger(__name__)


@app.route('/send_gcode', methods=['POST'])
def send_gcode() -> jsonify:
	"""
	Endpoint to send a G-code command to Marlin board.

	:return: JSON response with success message or error
	:rtype: flask.Response
	:raises KeyError: If no G-code is received in request
	:raises serial.SerialException: If a serial communication error occurs
	:raises Exception: If an unexpected error occurs
	"""
	gcode = request.json.get('gcode').strip()
	if not gcode:
		logger.error("No G-code received in request.")
		return jsonify({"error": "No G-code received"}), 400

	try:
		marlin_serial = MarlinSerial('/dev/ttyACM0')

		response = marlin_serial.send_gcode(gcode)
		response = response.decode('utf-8').replace('ok\n', '').strip()

		marlin_serial.close()

		logger.info(f"G-code '{gcode}' executed successfully.")
		return jsonify({"response": response}), 200
	except serial.SerialException as e:
		logger.error(f"SerialException: {str(e)}")
		return jsonify({"error": "Serial communication error"}), 500
	except Exception as e:
		logger.error(f"Unexpected error: {str(e)}")
		return jsonify({"error": "An unexpected error occurred"}), 500


@app.route('/status', methods=['GET'])
def status() -> jsonify:
	"""
	Endpoint to check the status of Marlin board.

	:return: JSON response with status message
	:rtype: flask.Response
	"""
	logger.info("Status check requested.")
	return jsonify({"message": "Marlin is ready."}), 200


@app.route('/encoder_status', methods=['GET'])
def encoder_status() -> jsonify:
	global enc
	"""
	Endpoint to get x, y encoder values.

	:return: JSON response with status message
	:rtype: flask.Response
	"""
	x = enc.read_counter(EncoderAxis.ENCODER_AXIS_X)
	y = enc.read_counter(EncoderAxis.ENCODER_AXIS_Y)
	return jsonify({"x": x, "y": y}), 200
	

if __name__ == '__main__':
	app.run(host='0.0.0.0', port=5000)

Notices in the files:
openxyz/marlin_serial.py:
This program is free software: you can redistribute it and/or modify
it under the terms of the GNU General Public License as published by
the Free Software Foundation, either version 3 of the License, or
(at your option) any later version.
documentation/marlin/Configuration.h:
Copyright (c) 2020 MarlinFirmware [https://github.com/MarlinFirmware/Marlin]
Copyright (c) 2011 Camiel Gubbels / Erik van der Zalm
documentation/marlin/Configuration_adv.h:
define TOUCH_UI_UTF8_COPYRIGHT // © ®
